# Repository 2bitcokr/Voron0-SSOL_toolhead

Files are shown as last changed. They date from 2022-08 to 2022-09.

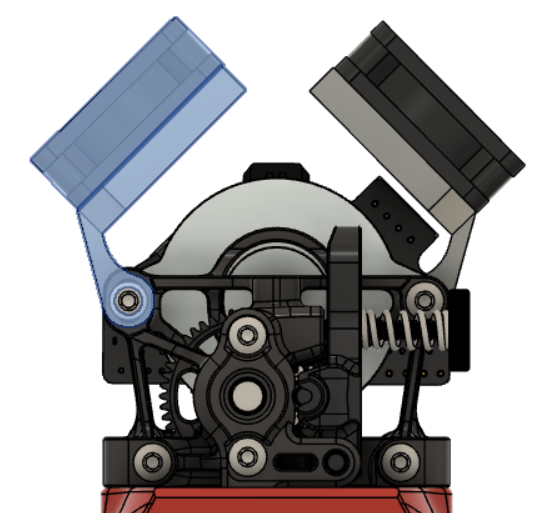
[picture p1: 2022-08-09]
image/FAN.png

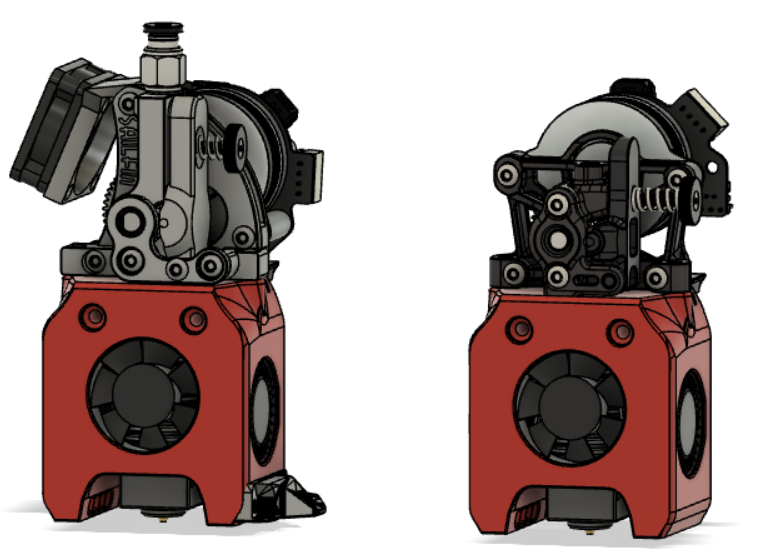
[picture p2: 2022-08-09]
image/BType_Sailfin_SherpaMini.png

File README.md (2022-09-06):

# Voron0-SSOL_toolhead
Vzero Toolhead Design 

This Design Based on the https://github.com/PrintersForAnts/Mini-AfterSherpa 

(Many parts are the same, mostly compatible with each other, with some modifications.)
ALL2

Supports 
V0 / V0.1 

recommended to apply 3MOD

MGN9C MOD (Need Changed X_carrage)

I only tested this on the MGN9C. recommend 9C rail MOD.

Klicky https://github.com/jlas1/Klicky-Probe

FANsaver https://github.com/VoronDesign/VoronUsers/tree/master/printer_mods/jappaj/FanSaver

# Printing Setting.
Same VORON PARTS setting
(infill 40% , 4wall )

X_Carriage is MGN7H (original) / MGN9C MOD 

ALL = All compatible ... But EasyCrack.. Need Infill 100% or METAL or SLM   (Lgxlite only All Version)

Safe to use a carriage that fits the extruder.



#BOM
Need some extra bolts and nuts.
(Most used as before BOM item)
Most use M3 bolts,
If the hole is large , insert nut (M3x5x4 insert 
Insertnut

# Surpport  Hotend 
Hotend

-V6 DUCT = V6 / REVO SIX /  NFZone V6 / Trianglelab,Mellow V6 / Slice Copperhead(groove) / Phaetus BMO 

-Micro Duct = V6Micro(threaded) / REVO micro 

-Dragon Duct = Trianglelab(Phaetus) Dragon / DragonFly BMO 

-Mosquito Duct = Slices Mosquito / NFCrazy 

Most recommended V6+CHC(trianglelab) Or NFZone+CHC is BEST .

Not recommend Mosquito,NFCrazy (It can kill a blowerfan. heatsink structure is Near to 3010blowerFAN.)

# Surpport Extruder
Duct A and duct B are not compatible.
(B ducts are not fitted with Orbiter. )

-A DUCT (USED Big Gear , New Extruder !!)

recommend  OrbiterV2,LGXLite good performance

bduct

LDO Orbiter V2.0
https://orbiterprojects.com/orbiter-v2-0/

Bontech LGX Lite! (Lgxlite is B Dcut Recommend)
https://www.bondtech.se/product/lgx-lite-extruder-no-motor/

-B DUCT (can use before BMG(MiniAB) gears.)

Bontech LGX Lite! (Bduct type Recommend)
https://www.bondtech.se/product/lgx-lite-extruder-no-motor/

SherpaMini
https://github.com/Annex-Engineering/Sherpa_Mini-Extruder

Sailfin (origianl version = Not compatible EBB36,SHT36,RHT36 )
https://github.com/CroXY3D/Sailfin-Extruder

Sailfin (2bitversion = compatible RHT36,EBB36,SHT36  ) 
sailfin

I made some changes to the sailfin extruder design.

Change gear alignment

Change bolt, insertnut position

Change shaft to bolt,insertnut(If you are changing from an existing miniAB, there is no shaft.)

Use PC4-M6 (option) (Have you ever experienced the Teflontube coming off when insert filament? I always modify tubefittings on all extruders.

# FAN MOUNT
If you use CanBUS(EBB,SHT36) , RHT expansion board

Need Extender Board cooling .

If Nofan, MCU temperature is 80~90 ℃.

USED FAN, MCU temperature is 60~70 ℃. ( Chamber Temperature+10℃)

Fan mounts are 2 STLs. (defualt,Mirror)

FAN cooling both the motor and the board.

Test results are very good with 1FAN.

AType_OrbiterV2_LGXLite
FAN
FAN2

Also compatible with MiniAB 
KakaoTalk_20220809_221840444

# Fansaver
FANsaver https://github.com/VoronDesign/VoronUsers/tree/master/printer_mods/jappaj/FanSaver

Fansaver is need for 3010blower fans.

I made some modify for V6 and Dragon.

And, NFzone can be use 3010Fan.

modify fansaver for 3010fan.
fansaver

# CanBUS / Toolheadboard

EBB36 / SHT36 / ★RHT36★ model is

It's really optimized for Vzero.

If you want to replace multiple toolheads

If you use the Toolheadboard on all tool heads,

The toolhead can be replaced in less than Just 1 minute.

KakaoTalk_20220809_202830313
KakaoTalk_20220809_202830313_02

KakaoTalk_20220809_202830313_01
KakaoTalk_20220809_202830313_03
KakaoTalk_20220809_221107363

ductzzz

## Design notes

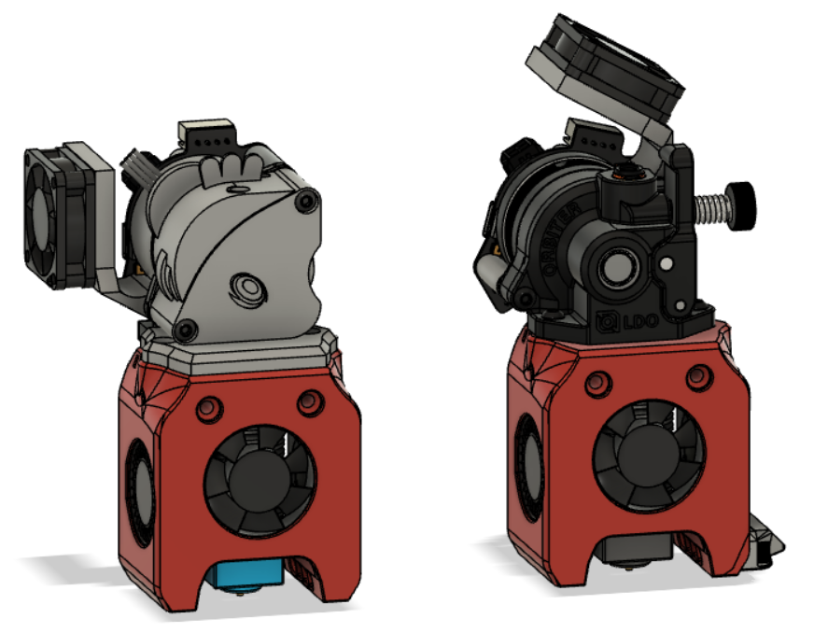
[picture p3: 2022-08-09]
image/AType_OrbiterV2_LGXLite.png

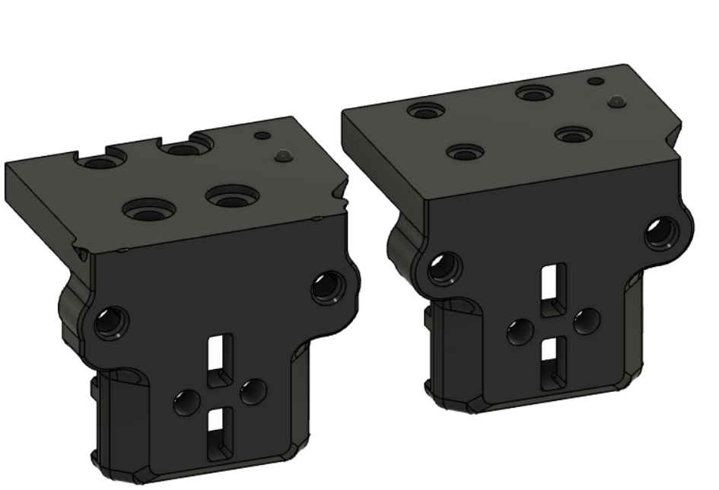
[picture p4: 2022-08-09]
image/X_carriage.png

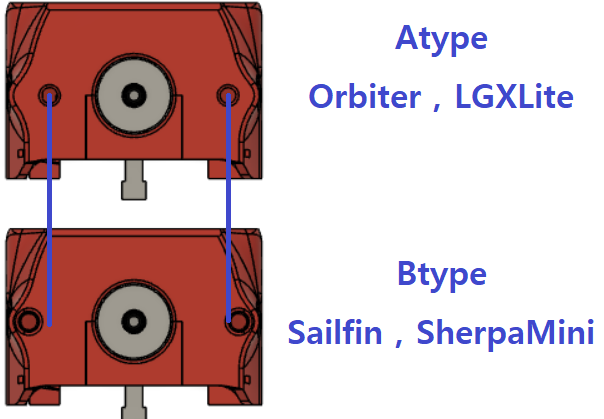
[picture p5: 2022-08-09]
image/AorB.png

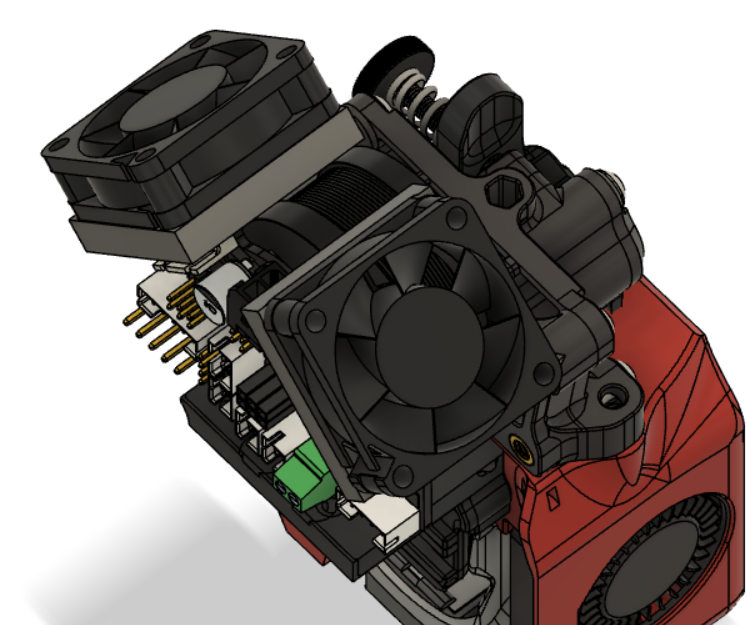
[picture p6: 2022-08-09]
image/FAN2.png

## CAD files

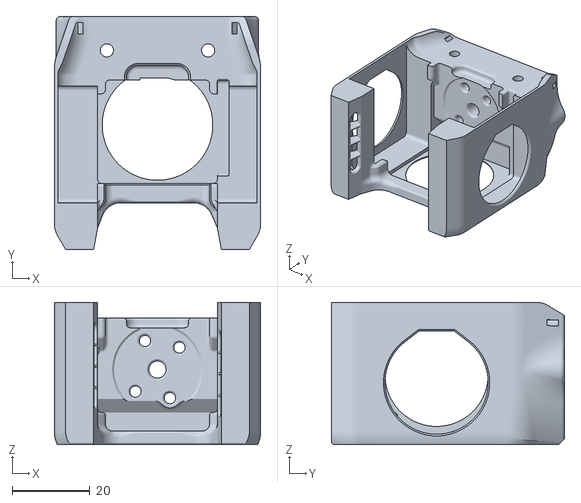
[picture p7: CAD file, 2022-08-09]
STL/DUCT/Dragon/A_DUCT_Dragon v2.stl
53.0 x 59.9 x 36.5

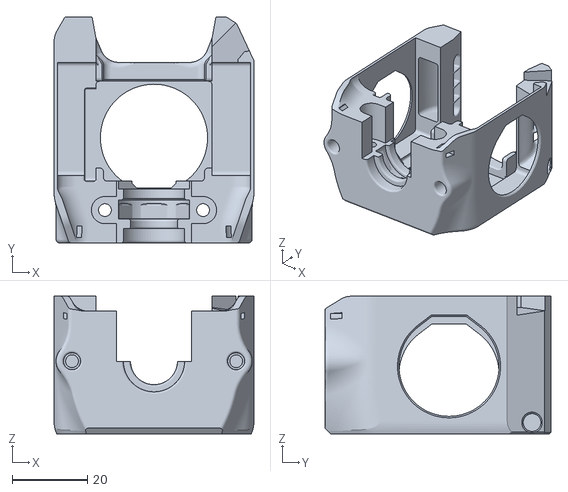
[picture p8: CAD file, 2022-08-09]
STL/DUCT/Micro/B_DUCT_Micro_Klicky v1.stl
53.0 x 59.9 x 36.5

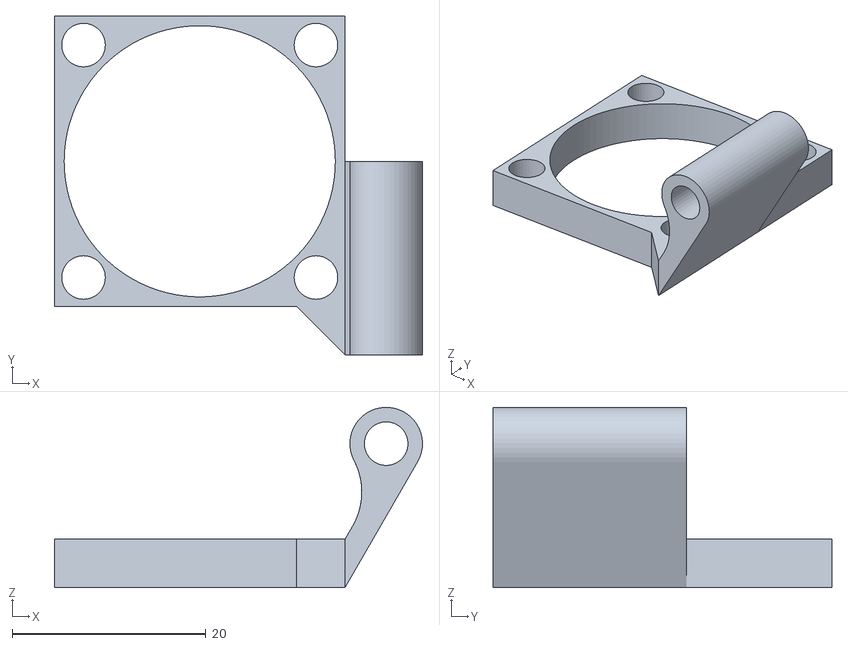
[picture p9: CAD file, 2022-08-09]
STL/FanMount.stl
38.0 x 35.0 x 18.6

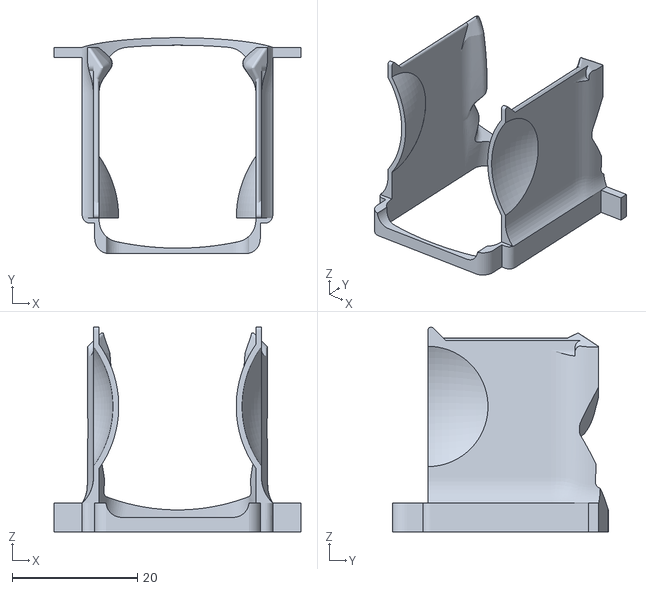
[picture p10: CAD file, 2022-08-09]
STL/FanSaver/FanSaver_AddAir.stl
39.4 x 34.4 x 32.6

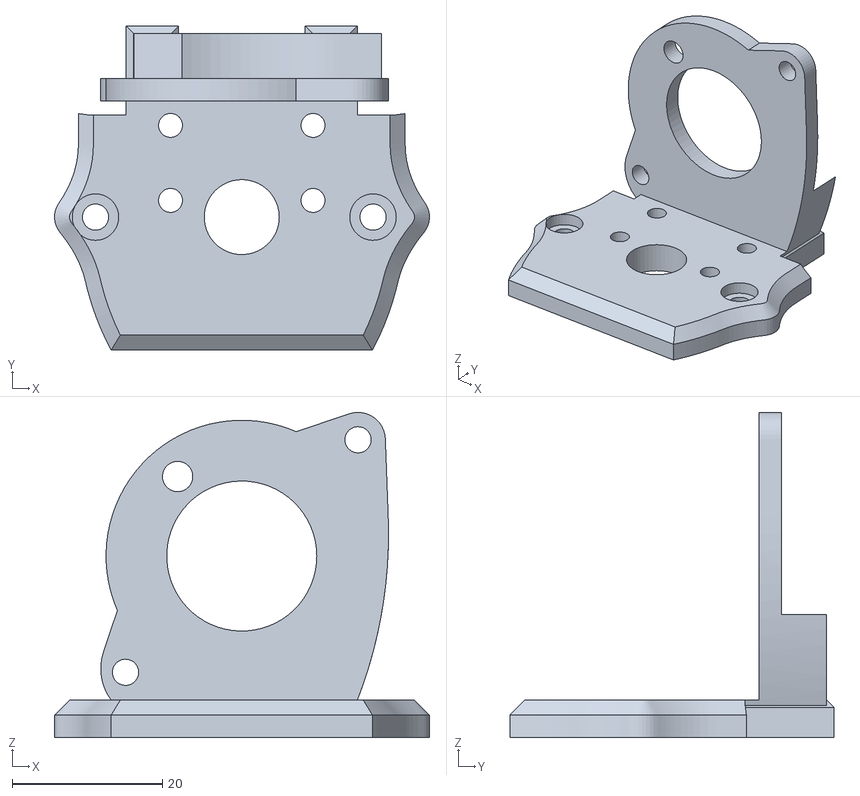
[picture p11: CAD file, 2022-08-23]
STL/LGXLite_mount/ADuct_LGXlite_back.stl
50.0 x 43.2 x 43.3

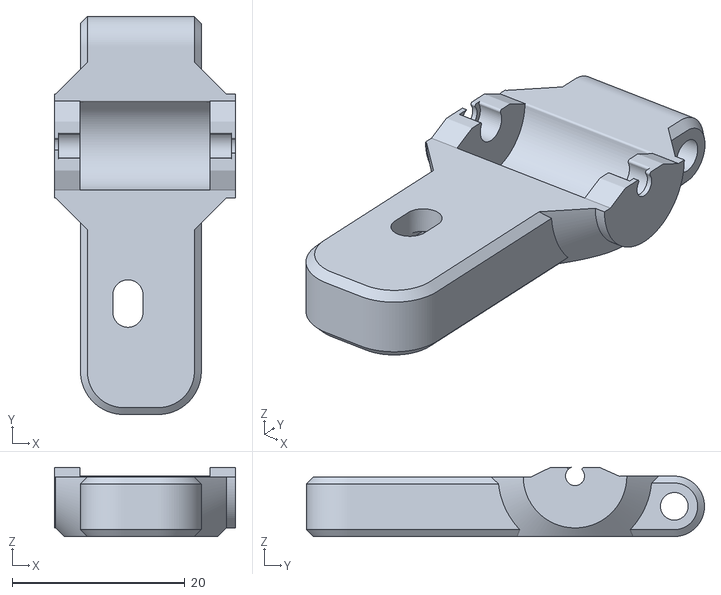
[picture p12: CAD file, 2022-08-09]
STL/Sailfin_extruder/Original/Lever.stl
21.0 x 46.1 x 8.00

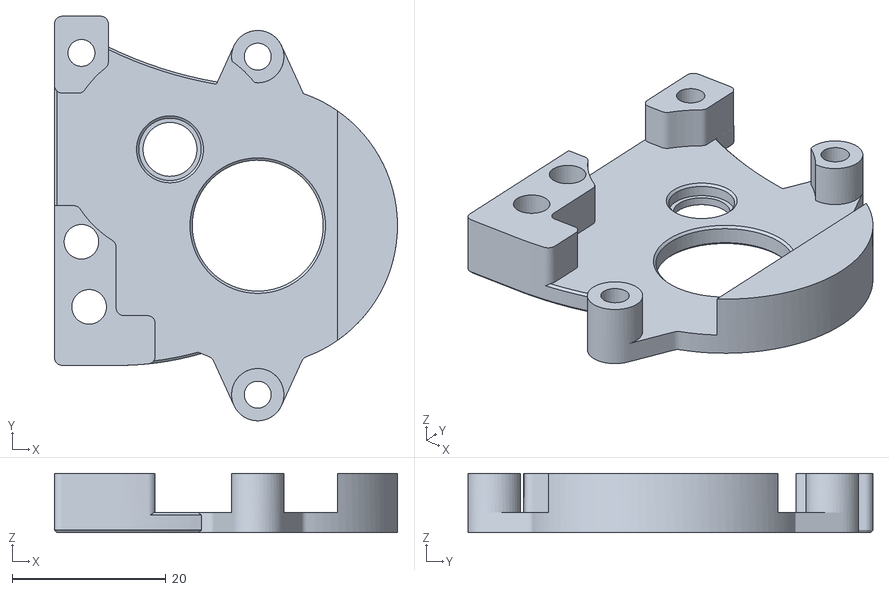
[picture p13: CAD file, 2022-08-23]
STL/Sailfin_extruder/sailfin/sailfin_rear.stl
44.5 x 52.6 x 7.67

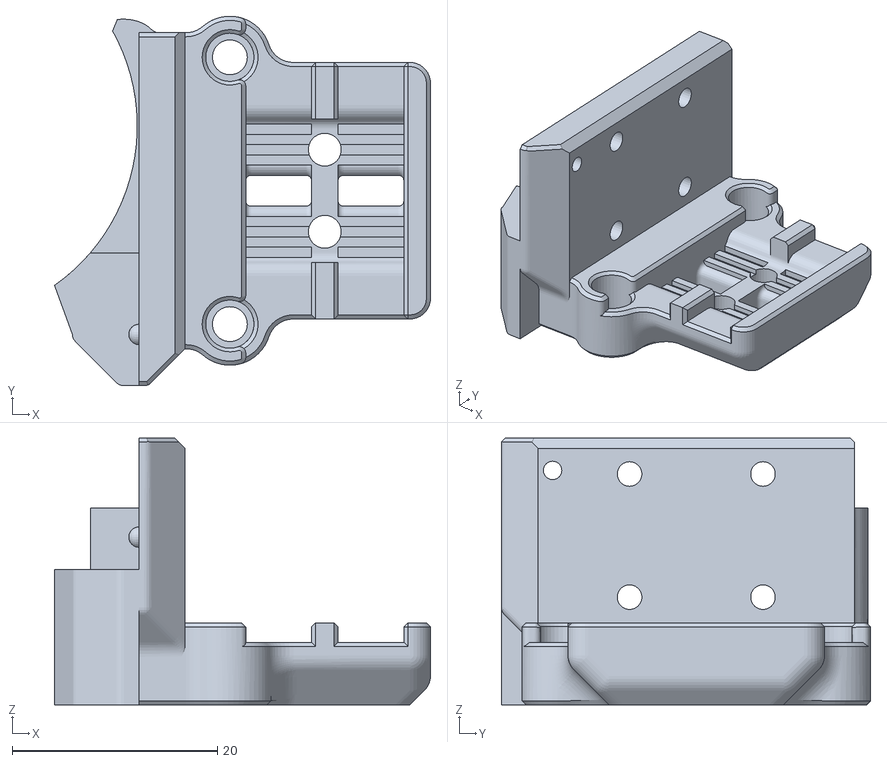
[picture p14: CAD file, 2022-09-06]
STL/Xcarriage/X_Carriage_7H_ForOrbiterV2.stl
36.6 x 36.0 x 26.0

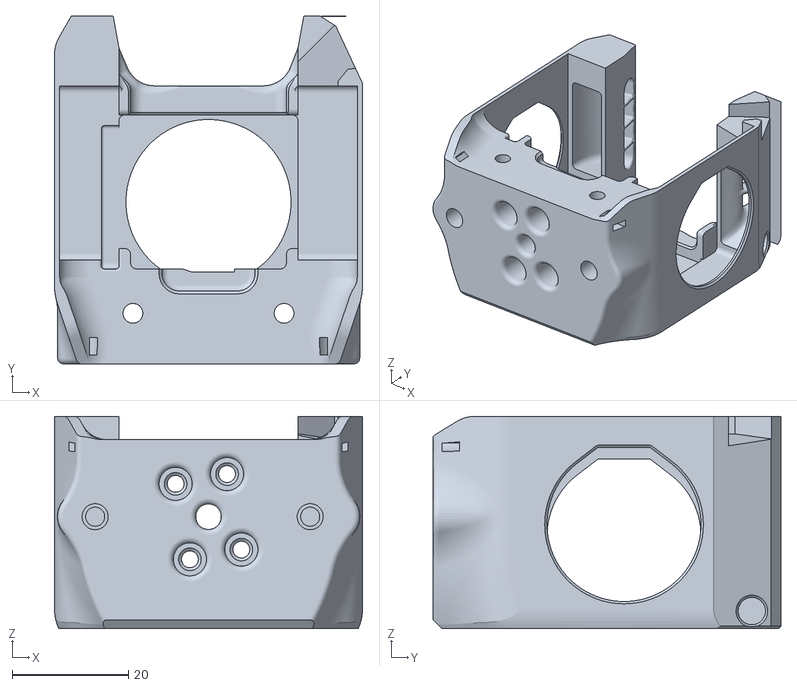
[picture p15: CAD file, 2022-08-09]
STL/DUCT/Dragon/A_DUCT_Dragon_Klicky v1.stl
53.0 x 59.9 x 36.5

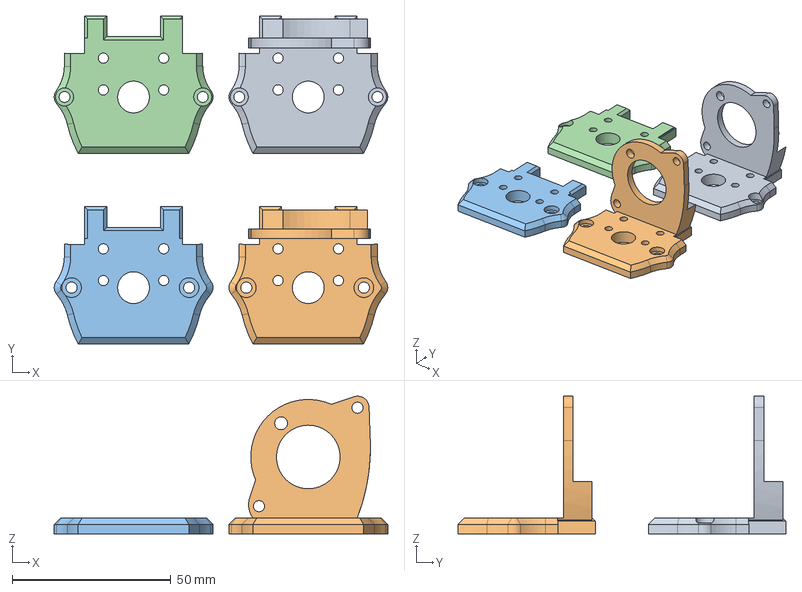
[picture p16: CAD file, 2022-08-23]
STL/LGXLite_mount/LGXlite_mount v0 v2.step
105.0 x 103.2 x 43.3 mm
Bduct_lgxLite_Back v1
Aduct-lgxlite_Back v2
Aduct-lgxLite_Noback v1

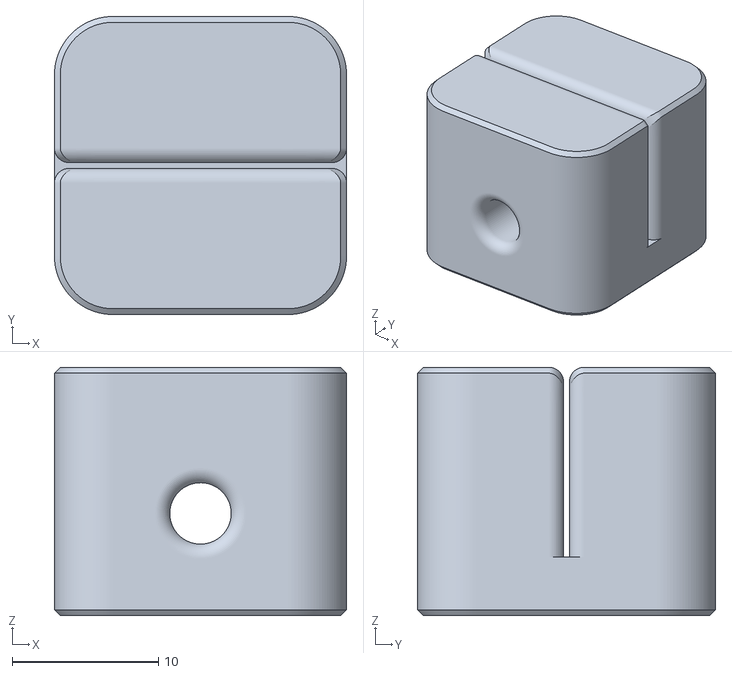
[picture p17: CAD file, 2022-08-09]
STL/Sailfin_extruder/Original/Sailfin_PTFE_Cut_Guide.stl
20.0 x 20.4 x 17.0

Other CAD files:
STL/DUCT/Mosquito/B_DUCT_mosquito_30mmFAN v3.stl
STL/DUCT/V6/B_DUCT_V6 v6.stl
STL/DUCT/Micro/A_DUCT_Micro v1.stl
STL/DUCT/Mosquito/B_DUCT_mosquito v3.stl
STL/DUCT/V6/A_DUCT_V6 v2.stl
STL/FanMount_Mirror.stl
STL/FanSaver/FanSaver_Defualt.stl
STL/DUCT/Dragon/B_DUCT_Dragon v2.stl
STL/DUCT/Dragon/B_DUCT_Dragon_Klicky v1.stl
STL/DUCT/Micro/A_DUCT_Micro_Klicky v1.stl
STL/DUCT/Micro/B_DUCT_Micro v1.stl
STL/DUCT/Micro/Micro_Bracket.stl
STL/DUCT/Micro/Micro_Bracket_2.stl
STL/DUCT/Micro/Micro_Bracket_holder.stl
STL/DUCT/Mosquito/A_DUCT_mosquito v1.stl
STL/DUCT/Mosquito/A_DUCT_mosquito_30mmFAN v2.stl
STL/DUCT/Mosquito/A_DUCT_mosquito_30mmFAN_Klicky v2.stl
STL/DUCT/Mosquito/A_DUCT_mosquito_Klicky v1.stl
STL/DUCT/Mosquito/B_DUCT_mosquito_30mmFAN_Klicky v1.stl
STL/DUCT/Mosquito/B_DUCT_mosquito_Klicky v1.stl
STL/DUCT/V6/A_DUCT_V6_Klicky v1.stl
STL/DUCT/V6/B_DUCT_V6_Klicky v1.stl
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
